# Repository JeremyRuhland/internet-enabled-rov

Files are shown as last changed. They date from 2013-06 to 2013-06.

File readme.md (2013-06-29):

Internet Enabled ROV
====================

Theory
------

The ROV will be connected to the surface by cat5 ethernet cable, carrying data and PoE at 12-48 volts depending on what power supply I find.

The underwater component will contain a motherboard, power converter and ip camera.

The motherboard contains a passive ethernet hub, connections to the power converter, microcontroller and motor drivers. The system can be programmed by usb connection.

When the motorboard's ip address is visited in a web browser, it responds with a simple html page showing instructions and a live updating camera feed. Pressing the WASD, QE and up/down arrow keys will send GET requests to the onboard webserver that will control the motor drivers. There is also a checkbox that will control an led array for increased lighting.

ROV Design
----------

The ROV will have four motors, one each for movement in the X, Y and Z axises and one for rotation of the robot.

All electronics will be encased in a waterproofed pvc pipe that will form the body of the ROV with a window endcap on one side and 5 waterproofed electrical connections on the other. Bits of foam will be used to achieve neutral density.

Motors will be standard brushed dc, placed inside pill bottles filled with paraffin and marine jelly for waterproofing. Propellers will be whatever I can get my hands on.

Embedded Webserver
------------------

Code for the embedded server is based off examples from jcw's [ethercard project](https://github.com/jcw/ethercard).

The javascript keyboard interface was inspired by a number of online tutorials and compressed to minimal size using google's [Closure Compiler](http://closure-compiler.appspot.com/).

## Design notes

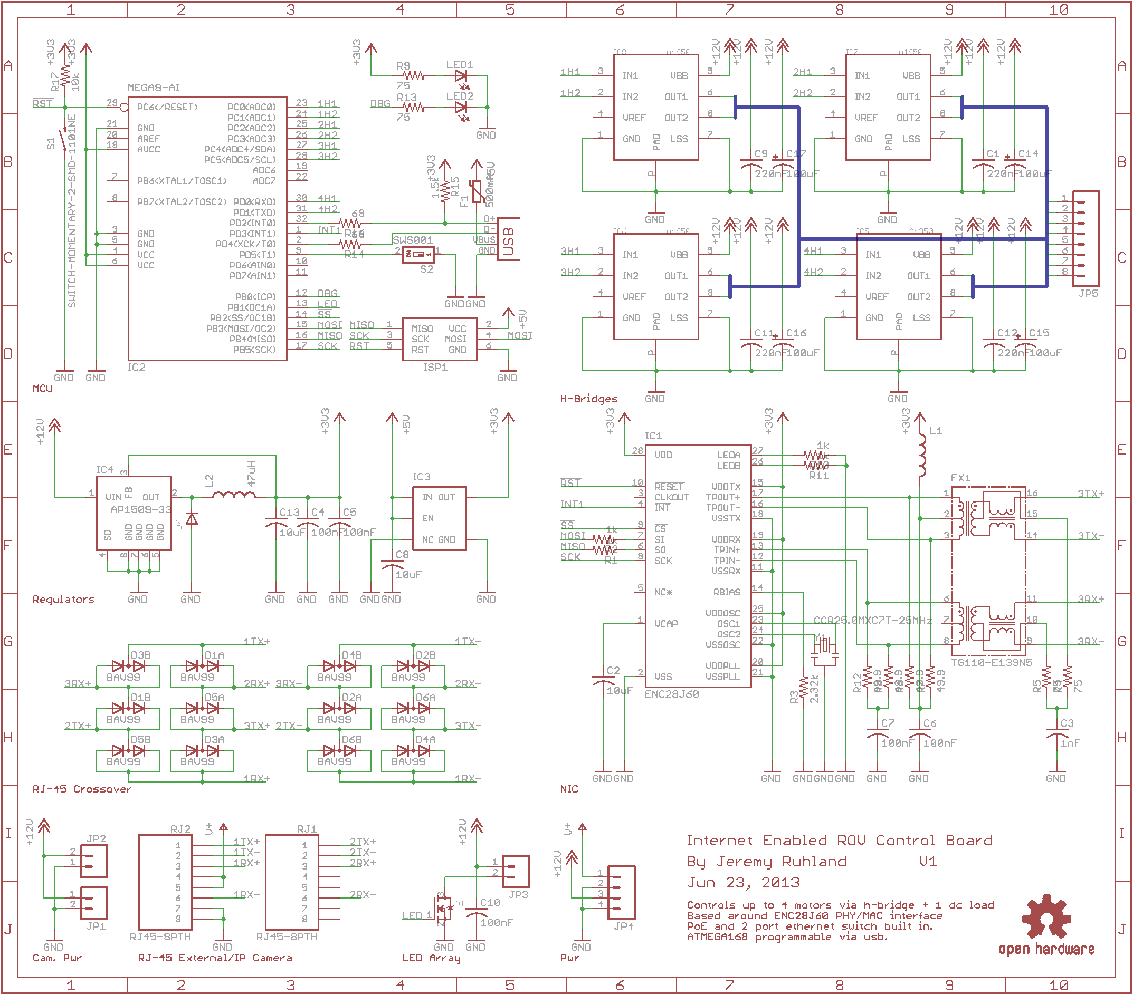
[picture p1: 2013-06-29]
internet_enabled_rov.sch.png

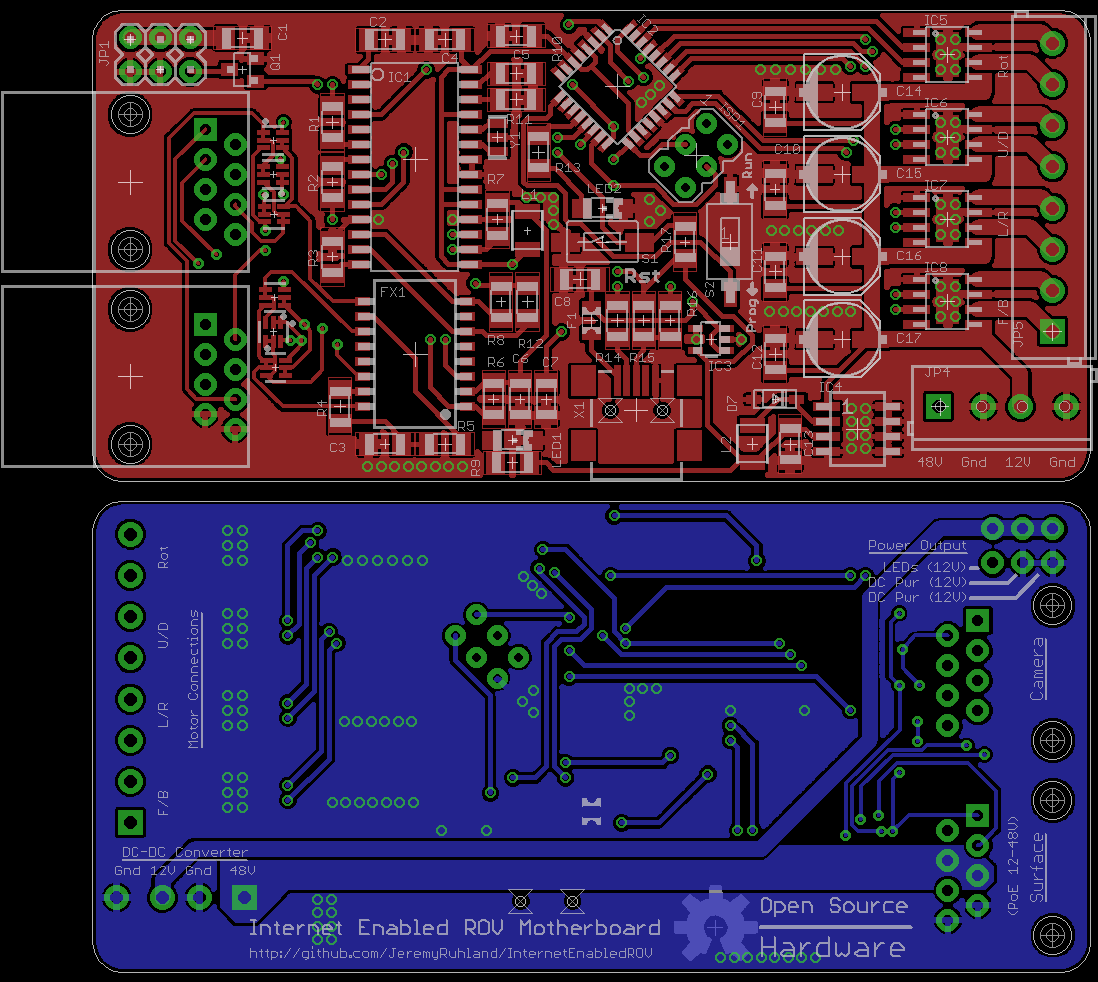
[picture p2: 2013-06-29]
internet_enabled_rov.brd.png

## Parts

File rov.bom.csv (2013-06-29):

Qty | Digikey Part Number | Value | Device | Parts
4 | 1276-1106-1-ND | 220nF | C-USC1206 | C1,C9,C11,C12
4 | PCE4238CT-ND | 100uF | CAP_POLD | C14,C15,C16,C17
3 | 399-8013-1-ND | 10uF | C-USC1206 | C2,C8,C13
1 | 1276-1772-1-ND | 1nF | C-USC1206 | C3
5 | 1276-1007-1-ND | 100nF | C-USC1206 | C4,C5,C6,C7,C10
6 | 568-8205-1-ND |  | BAV99 | D1,D2,D3,D4,D5,D6
1 | MBR130LSFT1GOSCT-ND |  | DIODESOD-123 | D7
1 | 507-1517-1-ND | 500mA | FUSE_PTC-0805 | F1
1 | 507-1468-1-ND |  | TG110-E139N5 | FX1
1 | ENC28J60-I/SO-ND |  | ENC28J60 | IC1
1 | ATMEGA168A-AU-ND | MCU | MEGA8-AI | IC2
1 | MCP1824T-3302E/OTCT-ND | 3.3V | V_REG_SOT23-5 | IC3
1 | AP1509-33SGDICT-ND | 3.3V | AP1509 | IC4
4 | 620-1400-1-ND |  | A4950 | IC5,IC6,IC7,IC8
1 | ED2742-ND | 3.5MM | M04SCREW_LOCK | JP4
1 | A98041-ND | 3.5MM | M08SCREW_LOCK | JP5
1 | CM322522-100KLCT-ND | FERRITE BEAD | INDUCTOR1210 | L1
1 | 587-1627-1-ND | 47uH | INDUCTOR1210 | L2
2 | 475-1416-1-ND | RED | LEDCHIPLED_1206 | LED1,LED2
1 | IRLML6344TRPBFCT-ND | N-CH 30V 5A FET | MOSFET-NREFLOW | Q1
4 | RMCF1206FT1K00CT-ND | 1k | R-US_R1206 | R1,R2,R10,R11
2 | RMCF1206FT68R0CT-ND | 68 | R-US_R1206 | R14,R16
1 | RMCF1206FT1K50CT-ND | 1.5k | R-US_R1206 | R15
1 | RMCF1206FT10K0CT-ND | 10k | R-US_R1206 | R17
1 | RMCF1206FT2K32CT-ND | 2.3k | R-US_R1206 | R3
4 | RMCF1206FT75R0CT-ND | 75 | R-US_R1206 | R4,R5,R9,R13
4 | RMCF1206FT49R9CT-ND | 49.9 | R-US_R1206 | R6,R7,R8,R12
2 | 609-1046-ND |  | RJ45-8PTH | RJ1,RJ2
1 | 450-1140-ND | 2-SMD-1101NE | SWITCH-MOMENTARY | S1
1 | 563-1004-1-ND | SWS001 | SWITCH-DIP | S2
1 | ED2992CT-ND |  | USBSMD | X1
1 | 445-1650-1-ND | 25MHz | RESONATORSMD | Y1

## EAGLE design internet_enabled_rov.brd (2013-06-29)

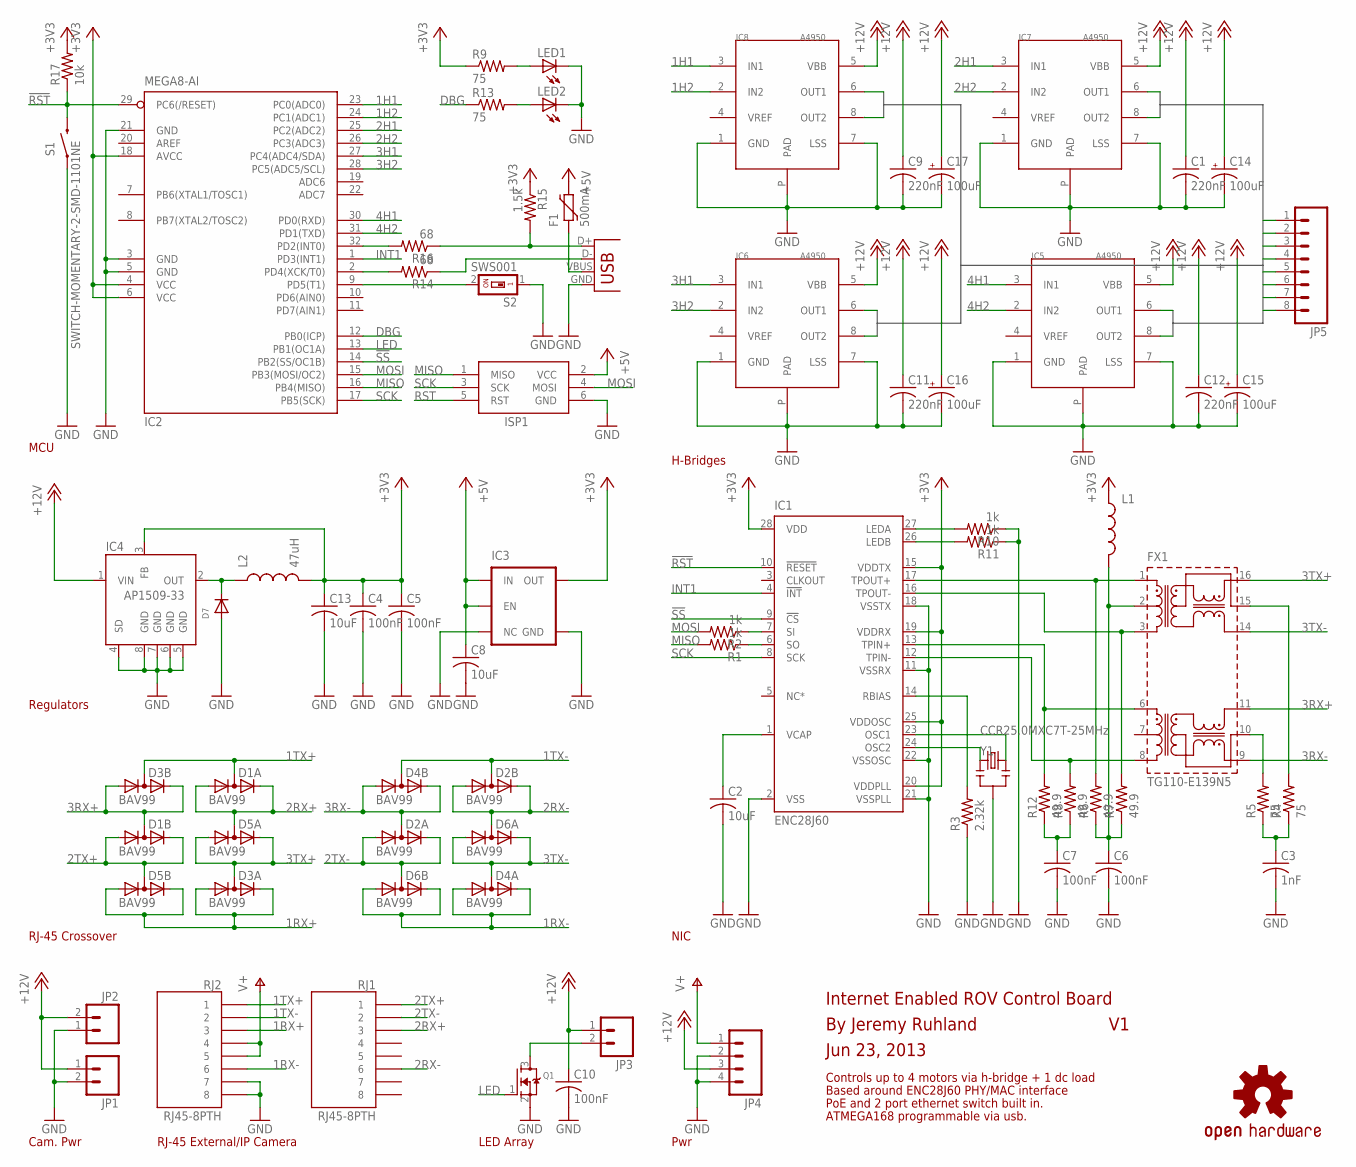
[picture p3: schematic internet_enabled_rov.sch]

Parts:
C1, C9, C11, C12: 220nF; C1206
C2, C8, C13: 10uF; C1206
C3: 1nF; C1206
C4, C5, C6, C7, C10: 100nF; C1206
C14, C15, C16, C17: 100uF; PANASONIC_D
D1, D2, D3, D4, D5, D6: BAV99; SOT363
D7: DIODESOD-123; SOD-123
F1: 500mA; PTC0805
FX1: TG110-E139N5; N5
IC1: ENC28J60; SO28W
IC2: MEGA8-AI; TQFP32-08
IC3: V_REG_TPS76433SOT23-5; SOT23-5
IC4: AP1509-33; SOP-8
IC5, IC6, IC7, IC8: A4950; SOIC-8-PAD
ISP1: AVRISP-6; AVRISP
JP1, JP2, JP3: M02LOCK; 1X02_LOCK
JP4: M04SCREW_LOCK; SCREWTERMINAL-3.5MM-4_LOCK
JP5: M083.5MM-8; SCREWTERMINAL-3.5MM-8
L1: INDUCTOR1210; 1210
L2: 47uH; 1210
LED1, LED2: LEDCHIPLED_1206; CHIPLED_1206
Q1: MOSFET-NREFLOW; SOT23
R1, R2, R10, R11: 1k; R1206
R3: 2.32k; R1206
R4, R5, R9, R13: 75; R1206
R6, R7, R8, R12: 49.9; R1206
R14, R16: 68; R1206
R15: 1.5k; R1206
R17: 10k; R1206
RJ1, RJ2: RJ45-8PTH; RJ45-8
S1: SWITCH-MOMENTARY-2-SMD-1101NE; TACTILE-SWITCH-1101NE
S2: SWS001; SMS-001
U$1: OSHW-LOGOL; OSHW-LOGO-L
X1: USBSMD; USB-MINIB
Y1: CCR25.0MXC7T-25MHz; RESONATOR-SMD

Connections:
1H1: IC2.23 (PC0(ADC0)), IC8.3 (IN1)
1H2: IC2.24 (PC1(ADC1)), IC8.2 (IN2)
1RX+: D3.1 (A), D3.2 (K), D5.4 (A), D5.5 (K), RJ2.3
1RX-: D4.1 (A), D4.2 (K), D6.4 (A), D6.5 (K), RJ2.6
1TX+: D1.6 (AK), D3.3 (AK), RJ2.1
1TX-: D2.3 (AK), D4.3 (AK), RJ2.2
2H1: IC2.25 (PC2(ADC2)), IC7.3 (IN1)
2H2: IC2.26 (PC3(ADC3)), IC7.2 (IN2)
2RX+: D1.1 (A), D1.2 (K), D5.6 (AK), RJ1.3
2RX-: D2.4 (A), D2.5 (K), D6.6 (AK), RJ1.6
2TX+: D1.4 (A), D1.5 (K), D5.3 (AK), RJ1.1
2TX-: D2.1 (A), D2.2 (K), D6.3 (AK), RJ1.2
3H1: IC2.27 (PC4(ADC4/SDA)), IC6.3 (IN1)
3H2: IC2.28 (PC5(ADC5/SCL)), IC6.2 (IN2)
3RX+: D1.3 (AK), D3.4 (A), D3.5 (K), FX1.11
3RX-: D2.6 (AK), D4.4 (A), D4.5 (K), FX1.9
3TX+: D3.6 (AK), D5.1 (A), D5.2 (K), FX1.16
3TX-: D4.6 (AK), D6.1 (A), D6.2 (K), FX1.14
4H1: IC2.30 (PD0(RXD)), IC5.3 (IN1)
4H2: IC2.31 (PD1(TXD)), IC5.2 (IN2)
!RST: IC1.10 (!RESET), IC2.29 (PC6(/RESET)), R17.1, S1.P$2 (2)
!SS: IC1.9 (!CS), IC2.14 (PB2(SS/OC1B))
+3V3: C4.1, C5.1, C13.1, IC1.15 (VDDTX), IC1.19 (VDDRX), IC1.20 (VDDPLL), IC1.25 (VDDOSC), IC1.28 (VDD), IC2.4 (VCC), IC2.6 (VCC), IC2.18 (AVCC), IC3.5 (OUT), IC4.3 (FB), L1.1, L2.2, R9.1, R15.1, R17.2
+5V: C8.1, F1.2, IC3.1 (IN), IC3.3 (EN), ISP1.2 (VCC)
+12V: C1.1, C9.1, C10.1, C11.1, C12.1, C14.+, C15.+, C16.+, C17.+, IC4.1 (VIN), IC5.5 (VBB), IC6.5 (VBB), IC7.5 (VBB), IC8.5 (VBB), JP1.1, JP2.2, JP3.1, JP4.3
DBG: IC2.12 (PB0(ICP)), R13.1
GND: C1.2, C2.2, C3.2, C4.2, C5.2, C6.2, C7.2, C8.2, C9.2, C10.2, C11.2, C12.2, C13.2, C14.-, C15.-, C16.-, C17.-, D7.A, IC1.2 (VSS), IC1.11 (VSSRX), IC1.18 (VSSTX), IC1.21 (VSSPLL), IC1.22 (VSSOSC), IC2.3 (GND), IC2.5 (GND), IC2.21 (GND), IC3.2 (GND), IC3.4 (NC), IC4.4 (SD), IC4.5 (GND), IC4.6 (GND), IC4.7 (GND), IC4.8 (GND), IC5.1 (GND), IC5.7 (LSS), IC5.P (PAD), IC6.1 (GND), IC6.7 (LSS), IC6.P (PAD), IC7.1 (GND), IC7.7 (LSS), IC7.P (PAD), IC8.1 (GND), IC8.7 (LSS), IC8.P (PAD), ISP1.6 (GND), JP1.2, JP2.1, JP4.2, JP4.4, LED1.C, LED2.C, Q1.2 (S), R3.1, R10.1, R11.1, RJ2.7, RJ2.8, S1.P$1 (1), S2.1, X1.GND, Y1.2
INT1: IC1.4 (!INT), IC2.1 (PD3(INT1))
LED: IC2.13 (PB1(OC1A)), Q1.1 (G)
MISO: IC2.16 (PB4(MISO)), ISP1.1 (MISO), R1.2
MOSI: IC2.15 (PB3(MOSI/OC2)), ISP1.4 (MOSI), R2.2
unnamed: IC1.6 (SO), R1.1
unnamed: F1.1, X1.VBUS
unnamed: LED1.A, R9.2
unnamed: LED2.A, R13.2
unnamed: IC1.7 (SI), R2.1
unnamed: D7.C, IC4.2 (OUT), L2.1
unnamed: FX1.10, R5.2
unnamed: FX1.15, R4.2
unnamed: IC2.32 (PD2(INT0)), R16.2
unnamed: IC2.2 (PD4(XCK/T0)), R14.2
unnamed: IC2.9 (PD5(T1)), S2.2
unnamed: JP3.2, Q1.3 (D)
unnamed: C3.1, R4.1, R5.1
unnamed: C7.1, R8.1, R12.1
unnamed: C6.1, FX1.2, L1.2, R6.1, R7.1
unnamed: FX1.3, IC1.16 (TPOUT-), R7.2
unnamed: FX1.1, IC1.17 (TPOUT+), R6.2
unnamed: FX1.8, IC1.12 (TPIN-), R8.2
unnamed: FX1.6, IC1.13 (TPIN+), R12.2
unnamed: R15.2, R16.1, X1.D+
unnamed: R14.1, X1.D-
unnamed: C2.1, IC1.1 (VCAP)
unnamed: IC1.14 (RBIAS), R3.2
unnamed: IC1.24 (OSC2), Y1.1
unnamed: IC1.23 (OSC1), Y1.3
unnamed: IC1.27 (LEDA), R10.2
unnamed: IC1.26 (LEDB), R11.2
OUT1: IC8.8 (OUT2), JP5.2
OUT2: IC8.6 (OUT1), JP5.1
OUT3: IC7.8 (OUT2), JP5.4
OUT4: IC7.6 (OUT1), JP5.3
OUT5: IC6.8 (OUT2), JP5.6
OUT6: IC6.6 (OUT1), JP5.5
OUT7: IC5.8 (OUT2), JP5.8
OUT8: IC5.6 (OUT1), JP5.7
RST: ISP1.5 (RST)
SCK: IC1.8 (SCK), IC2.17 (PB5(SCK)), ISP1.3 (SCK)
V+: JP4.1, RJ2.4, RJ2.5

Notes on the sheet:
RJ-45 External/IP Camera
LED Array
Pwr
Regulators
MCU
NIC
H-Bridges
RJ-45 Crossover
Cam. Pwr
Internet Enabled ROV Control Board
By Jeremy Ruhland
Based around ENC28J60 PHY/MAC interface
Controls up to 4 motors via h-bridge + 1 dc load
Jun 23, 2013
PoE and 2 port ethernet switch built in.
ATMEGA168 programmable via usb.

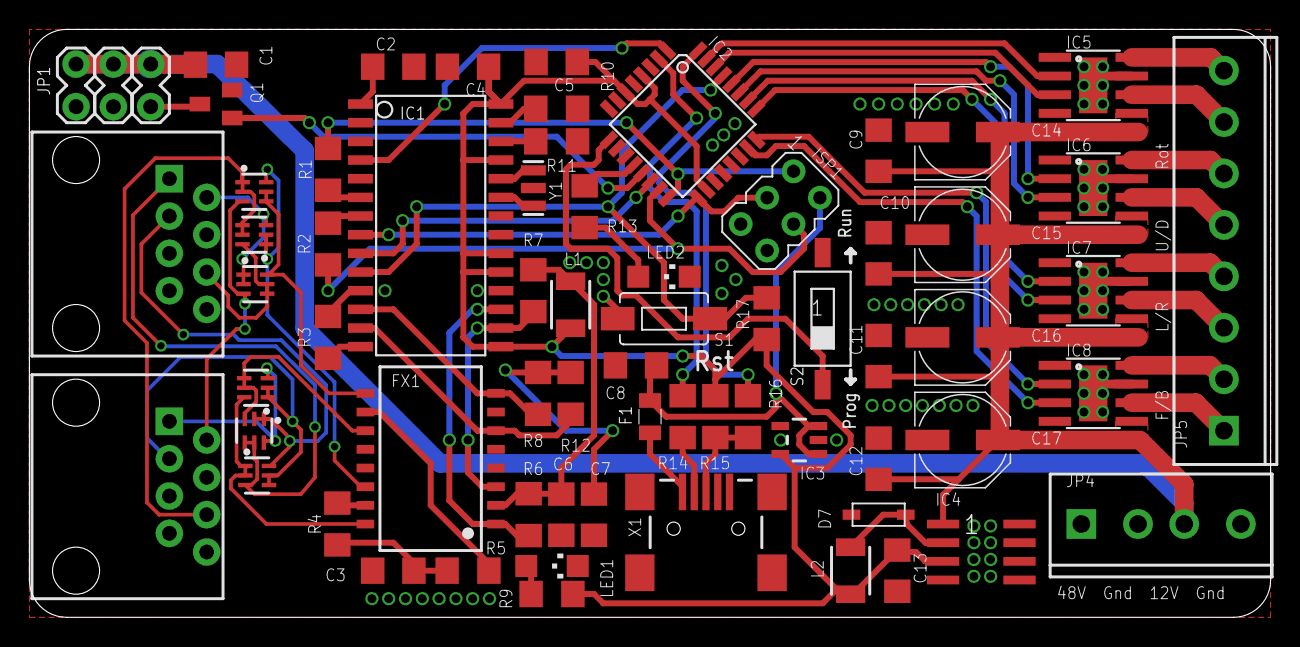
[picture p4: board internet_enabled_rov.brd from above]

Board: 2 copper layers, 84.5 x 40.0 mm, 69 parts (1 on the bottom side), 68 nets.

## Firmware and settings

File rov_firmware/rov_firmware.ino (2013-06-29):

// UDP firmware for internet enabled ROV
// By Jeremy Ruhland
// Based off example code by Brian Lee <cybexsoft@hotmail.com>

#define stopAllMotors() PORTC &= ~((1<<PC5)|(1<<PC4)|(1<<PC3)|(1<<PC2)|(1<<PC1)|(1<<PC0)); PORTD &= ~((1<<PD1)|(1<<PD0))
#define lightsOff() PORTB &= ~(1<<PB0)
#define lightsOn() PORTB |= (1<<PB0)
#define forwardThrust() PORTC |= (1<<PC0)
#define reverseThrust() PORTC |= (1<<PC1)
#define forwardReverseStop() PORTC &= ~((1<<PC1)|(1<<PC0)) 
#define starboardThrust() PORTC |= (1<<PC2)
#define portThrust() PORTC |= (1<<PC3)
#define starboardPortStop() PORTC &= ~((1<<PC3)|(1<<PC2))
#define diveThrust() PORTC |= (1<<PC4)
#define surfaceThrust() PORTC |= (1<<PC5)
#define diveSurfaceStop() PORTC &= ~((1<<PC5)|(1<<PC4))
#define clockwiseThrust() PORTD |= (1<<PD0)
#define anticlockwiseThrust() PORTD |= (1<<PD1)
#define clockwiseAnticlockwiseStop() PORTD &= ~((1<<PD1)|(1<<PD0))

#include <EtherCard.h>
#include <avr/eeprom.h>

// ethernet interface ip address
static byte myip[] = { 192,168,1,200 };
// ethernet interface mac address - must be unique on your network
static byte mymac[] = { 0x74,0x69,0x69,0x2D,0x30,0x31 };

byte Ethernet::buffer[1200];   // tcp/ip send and receive buffer
static BufferFiller bfill; // used as cursor while filling the buffer

char functionName[2];	// query key of sent command

char okHeader[] PROGMEM = 
    "HTTP/1.0 200 OK\r\n"
    "Content-Type: text/html\r\n"
    "Pragma: no-cache\r\n"
;

char indexPage[] PROGMEM = 
    "<html><b>ROV Web Interface</b>"
    "<table><tr><td><iframe width=\"480\" height=\"302\" src=\"http://www.ustream.tv/embed/9948292\?v=3\"></iframe></td>"
    "<td><hr width=1 size=250></td><td>Keyboard controlls:<br>Arrow Keys and<br>A (Ascend)<br>Z (Descend)<br><br><label><input type=\'checkbox\' onchange=\'e(this);\'>Enable Lighting</label></td></tr></table>"
    "<script>var a;var b={};var i=document.createElement(\"img\");function c(e){if(a&&a.keyCode==e.keyCode)return;if(!e)e=window.event;a=e;b[e.keyCode]=true;if(e.keyCode==65)i.src=\"\?c=1\";if(e.keyCode==90)i.src=\"\?c=2\";if(e.keyCode==37)i.src=\"\?c=4\";if(e.keyCode==39)i.src=\"\?c=5\";if(e.keyCode==38)i.src=\"\?c=7\";if(e.keyCode==40)i.src=\"\?c=8\";if(e.keyCode==33)i.src=\"\?c=c\";if(e.keyCode==34)i.src=\"\?c=d\";}function d(e){a=null;delete b[e.keyCode];if(!e)e=window.event;if(e.keyCode==65||e.keyCode==90)i.src=\"\?c=3\";if(e.keyCode==37||e.keyCode==39)i.src=\"\?c=6\";if(e.keyCode==38||e.keyCode==40)i.src=\"\?c=9\";if(e.keyCode==33||e.keyCode==34)i.src=\"\?c=e\";}function e(cb){if(cb.checked==true)i.src=\"\?c=a\";else i.src=\"\?c=b\";}document.onkeydown=c;document.onkeyup=d;</script></html>"
;

static void homePage(BufferFiller& buf) {
    buf.emit_p(indexPage, okHeader);
}

static void commandParse(const char* data, BufferFiller& buf) {
    // execute command, if present
    switch(functionName[0]) {
	case '0':	// All motors off
                stopAllMotors();
		break;
	case '1':	// Up
	            surfaceThrust();
		break;
	case '2':	// Down
	            diveThrust();
		break;
	case '3':	// Up/down off
	            diveSurfaceStop();
		break;
	case '4':   // Left
	            portThrust();
		break;
	case '5':   // Right
	            starboardThrust();
		break;
	case '6':   // Left/right off
	            starboardPortStop();
		break;
	case '7':	// Fwd
	            forwardThrust();
		break;
	case '8':	// Back
	            reverseThrust();
		break;
	case '9':	// Fwd/back off
	            forwardReverseStop();
		break;
	case 'a':	// Lights on
	            lightsOn();
		break;
	case 'b':	// Lights off
	            lightsOff();
		break;
	case 'c':	// Rotate CW
	            clockwiseThrust();
		break;
	case 'd':	// Rotate CCW
	            anticlockwiseThrust();
		break;
    case 'e':   // Rotate off
                clockwiseAnticlockwiseStop();
        break;
	default:    // Emergency case, should never be entered
                stopAllMotors();
		break;
	}
}

void setup(){
    // Disable motors/lights
    PORTB &= ~(1<<PB1);
    PORTC &= ~((1<<PC5)|(1<<PC4)|(1<<PC3)|(1<<PC2)|(1<<PC1)|(1<<PC0));
    PORTD &= ~((1<<PD1)|(1<<PD0));
    // Set ouput ports correctly
    DDRB |= (1<<PB1);
    DDRC |= (1<<PC5)|(1<<PC4)|(1<<PC3)|(1<<PC2)|(1<<PC1)|(1<<PC0);
    DDRD |= (1<<PD1)|(1<<PD0);
    // Init ethernet system
    ether.begin(sizeof Ethernet::buffer, mymac);
    ether.staticSetup(myip);
}

void loop(){
    word len = ether.packetReceive();
    word pos = ether.packetLoop(len);
    // check if valid tcp data is received
    if (pos) {
        bfill = ether.tcpOffset();
        char* data = (char *) Ethernet::buffer + pos;
        // receive buf hasn't been clobbered by reply yet
        if (EtherCard::findKeyVal(data, functionName, 2, "c") != 0)
            commandParse(data, bfill);
        else
            homePage(bfill);
        ether.httpServerReply(bfill.position()); // send web page data
    }
}

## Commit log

2013-06-29 First commit, created repo
    [internet_enabled_rov.brd, internet_enabled_rov.sch, rov.bom.csv]
2013-06-29 Added pcb images.
    [internet_enabled_rov.brd]

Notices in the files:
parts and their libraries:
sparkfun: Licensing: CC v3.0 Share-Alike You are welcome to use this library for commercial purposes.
